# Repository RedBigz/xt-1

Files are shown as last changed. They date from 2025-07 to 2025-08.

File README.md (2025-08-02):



## IMPORTANT

- The JST PH connectors from the t-plugs to the supp. board need to have reverse connectors!

# XT-1





A modular CoreXY 3D Printer with a focus on repairability.

| [READ THE JOURNAL](./JOURNAL.md) | [READ CAD CREDITS](CAD_CREDITS.md) |
| --- | --- |

| A render of an XT-1 with a Benchy atop its bed | Gantry of an XT-1 |
| --- | --- |
| Close-up of the toolhead/bed of the XT-1 | Close-up of the bottom of the XT-1 |

## Who I am and why I made this

Hi, I'm May, a 15-year-old programmer and hardware enthusiast from Australia. I have spent the past few weeks developing a custom 3D printer based on the CoreXY motion system that allows for custom component bays to be inserted on the toolhead. I made this dovetail plug (t-plug) system to mimic the concept of [Framework](https://frame.work)'s laptop expansion bays. I believe expansion bays largely simplify repairs performed by consumers and allows for greater self-expression through custom designs that can be attached to the toolhead.

## What is this?

The XT-1 is a custom CoreXY 3D printer with two custom t-plug (as defined above) bays to transmit UART and 5V & 24V PWM signals for things such as:

- Accelerometers (not ADXL as they're SPI)
- Laser Diodes
- Fans

Here are some basic statistics for the printer:

- 2 t-plug bays
- 2WD CoreXY System
- 180x180x160 build volume
- ~360x360x420 external dimensions

# Gallery

## CAD Model

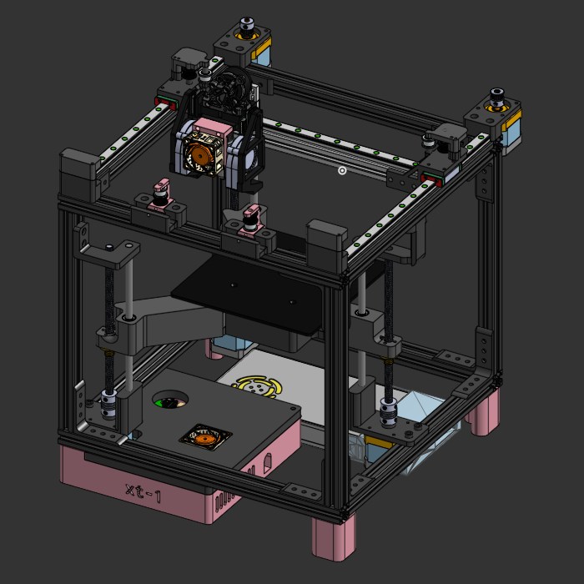
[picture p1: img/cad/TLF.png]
Top-Left-Front view of the XT-1

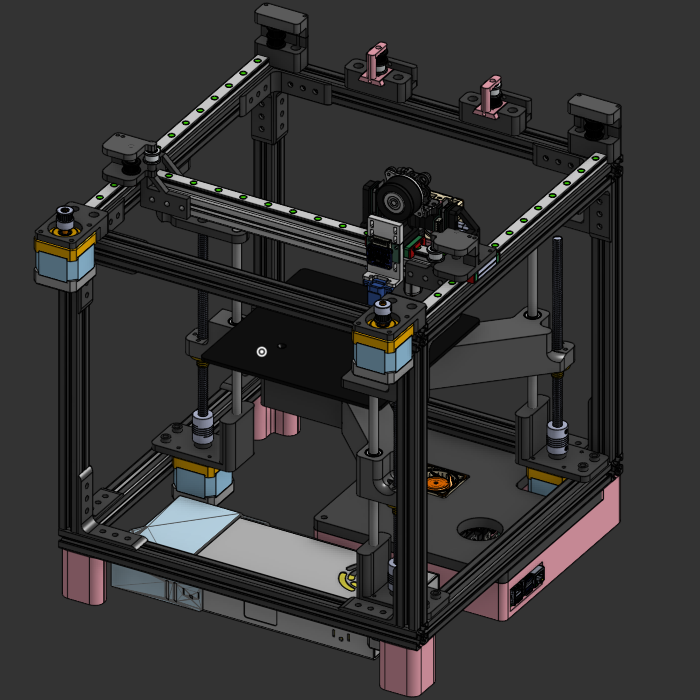
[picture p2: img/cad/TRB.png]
Top-Right-Back view of the XT-1


## Supplementary Board

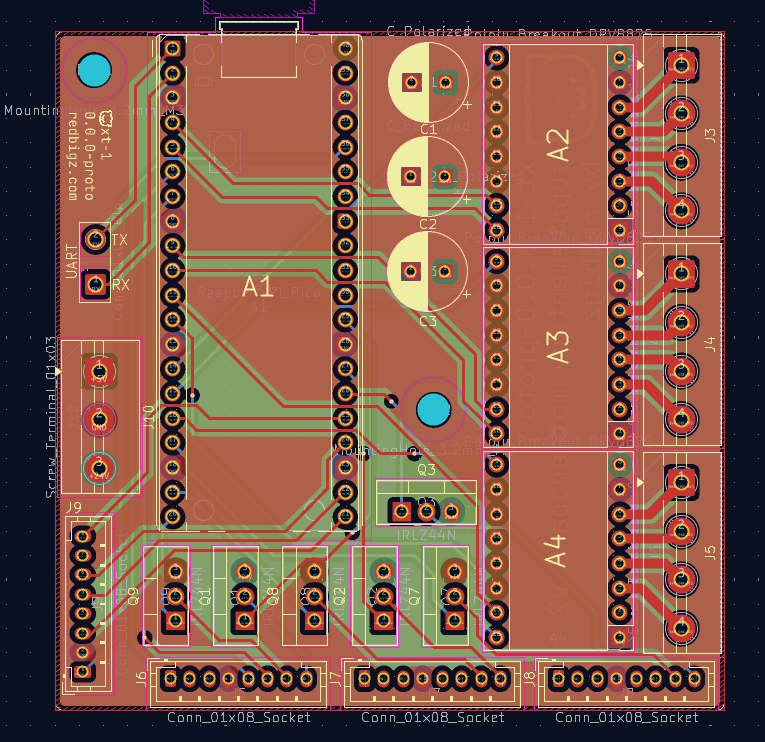
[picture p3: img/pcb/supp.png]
Pcbnew view of the Supplementary Board of the XT-1


## T-Plug

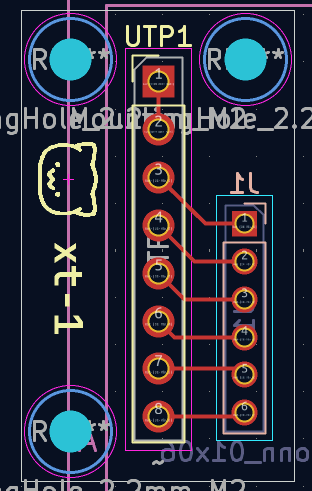
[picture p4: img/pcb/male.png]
Pcbnew view of the XT-1 male t-plug

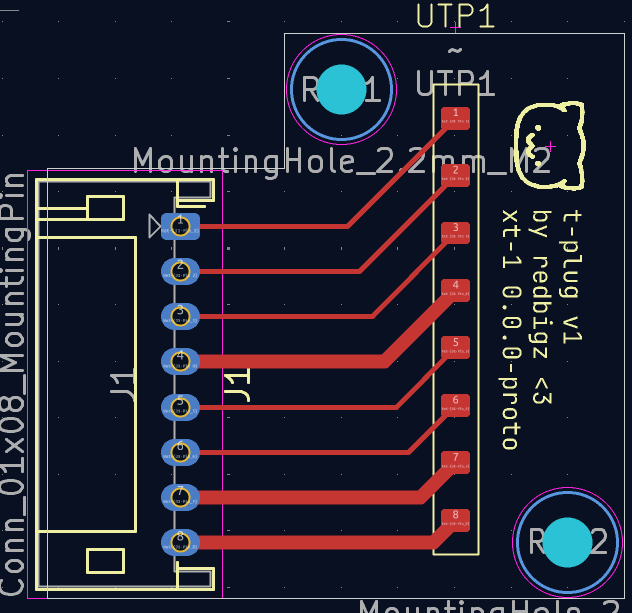
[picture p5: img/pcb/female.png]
Pcbnew view of the XT-1 female t-plug


# Building

## CAD Models

To export parts, open the model in OnShape [here](https://cad.onshape.com/documents/9bd0c3164ed27c6437ee23ee/w/6070e846ece5dc4f933b41e5/e/3b4b9a8834f82e5e0afe2787) (I would suggest plugging in your computer before downloading, the models are hundreds of megs and just rendering them has crashed my desktop RX 7800XT over 10 times when rendering the full assembly)

To find the _assembly_ in .STEP format, check the `asm` folder in this repo.

## Wiring Diagram

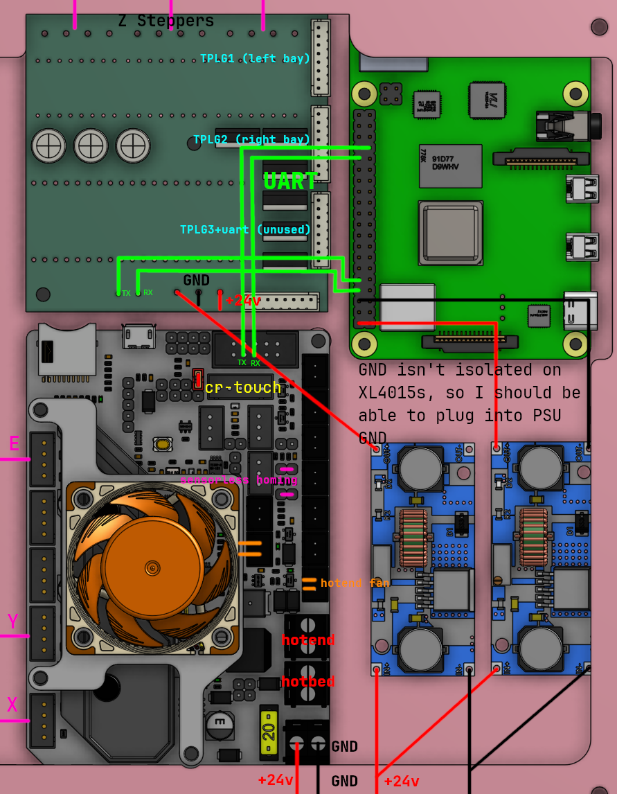
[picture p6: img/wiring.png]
An electronic wiring diagram of the XT-1


## Quick BOM

**Quick Note:** This BOM is made largely for Hack Club's [Highway grant program](https://highway.hackclub.com) and prices reference the sale price I am able to purchase each product at (as @ 29/07/2025) in AUD (with a AUD -> USD exchange rate of $0.66 per A$1).

| Manufacturer | Item | Size | Qty | Units | Unit Cost (AUD) | Cost (AUD) | Cost (USD) | Link |
| --- | --- | --- | --- | ----- | --- | --- | --- | --- |
| BIGTREETECH | BTT SKR Mini E3 V3 | - | 1 | each  | 52.51 | 52.51 | 34.66 | https://www.aliexpress.com/item/1005003519869375.html |
| JINGLIN | 5/lot 4-lead NEMA 17 | - | 1 | lot | 69.39 | 69.39 | 45.80 | https://www.aliexpress.com/item/1005008510880419.html |
| | 2/lot 5015 Turbo Fan | - | 1 | lot | 4.90 | 4.90 | 3.23 | https://www.aliexpress.com/item/32970914615.html |
| JINGLIN | 2/lot 4020 Fan | - | 1 | lot | 5.09 | 5.09 | 3.36 | https://www.aliexpress.com/item/32972111881.html |
| Ancufy | NEMA 14 + 1M cable | - | 1 | each  | 14.89 | 14.89 | 9.83 | https://www.aliexpress.com/item/1005006423228157.html |
| HighQ | 2/lot 2020 V-Slot Extrusions | 280mm | 2 | lot | 14.79 | 29.58 | 19.52 | https://www.aliexpress.com/item/1005007310271857.html |
| | | 320mm | 2 | lot | 15.89 | 31.78 | 20.97 | |
| | | 360mm | 2 | lot | 16.69 | 33.38 | 22.03 | |
| Magic Dragon | 2020 V-Slot Extrusions | 300mm | 1 | each  | 8.47 | 8.47 | 5.59 | https://www.aliexpress.com/item/1005004679698586.html |
| | MGN12 Linear Rail | 300mm | 1 | each  | 20.39 | 20.39 | 13.46 | https://www.aliexpress.com/item/1005003696820721.html |
| CHY CNC | 2/lot 8mm Linear Shaft (M4x8mm) | 200mm | 2 | lot | 16.29 | 32.58 | 21.50 | https://www.aliexpress.com/item/1005008854590053.html |
| SNWNYN | 2x MGN12H rails, 4x MGN Blocks | 200mm | 1 | lot | 34.59 | 34.59 | 22.83 | https://www.aliexpress.com/item/1005005966099152.html |
| 3D ManufacturinG | T8 Lead Screw + Nut | 200mm | 3 | each  | 5.49 | 16.47 | 10.87 | https://www.aliexpress.com/item/1005007457419235.html |
| ElectronicModule | D20L25 Lead Screw Coupler | - | 3 | each  | 2.76 | 8.28 | 5.46 | https://www.aliexpress.com/item/1005006456811778.html |
| Haldis | Gearset Kit | - | 1 | each  | 21.39 | 21.39 | 14.12 | https://www.aliexpress.com/item/1005004699143725.html |
| Lerdge | Lerdge iX 180mm Hotbed (Magnetic) | - | 1 | each  | 30.79 | 30.79 | 20.32 | https://www.aliexpress.com/item/1005005641707683.html |
| Good Luck Elec. Prod.  | 2/lot XL4015 | | 1 | lot | 6.21 | 6.21 | 4.10 | https://www.aliexpress.com/item/1005006823558141.html |
| TLZWLA | 10/lot 01x08 2.54mm Female Header Socket | - | 1 | lot | 2.16 | 2.16 | 1.43 | https://www.aliexpress.com/item/4001198421663.html |
| | 10/lot 01x20 2.54mm Female Header Socket | - | 1 | lot | 2.62 | 2.62 | 1.73 | |
| Unnamed | GY-291 ADXL345 Module | - | 1 | each  | 2.91 | 2.91 | 1.92 | https://www.aliexpress.com/item/1005007557329503.html |
| ICGOGO | 40/lot F-F DuPont Jumper Wires | 100mm | 1 | lot | 4.20 | 4.20 | 2.77 | https://www.aliexpress.com/item/1005002000655439.html |
| YouKeyi | 5/lot DRV8825 Module | - | 1 | lot | 9.99 | 9.99 | 6.59 | https://www.aliexpress.com/item/1005009321177962.html |
| USBO | IEC320 C14 Fused Switch | - | 1 | each  | 13.49 | 13.49 | 8.90 | https://www.aliexpress.com/item/4001315809458.html |
| Wurth Elektronik | 860040674004 100uF 50V | D8xL12mm | 10  | each  | 0.555 | 5.55 | 3.66 | https://au.mouser.com/ProductDetail/Wurth-Elektronik/860040674004 |
| NINDEJIN NINDEJIN | 50/lot M2x8mm Hex Wafer Head Screw | - | 1 | lot | 2.06 | 2.06 | 1.36 | https://www.aliexpress.com/item/1005008750192874.html |
| Don Eden | Pan Screws (PH) | 50pcs M3x5mm | 1 | lot | 2.82 | 2.82 | 1.86 | https://www.aliexpress.com/item/1005008709978631.html |
| | (note, 16mm screws are in place of 15mm screws due to lack of listings) | 50pcs M3x16mm | 1 | lot | 4.29 | 4.29 | 2.83 | |
| | | 50pcs M3x35mm | 1 | lot | 6.09 | 6.09 | 4.02 | |
| | | 20pcs M4x8mm | 1 | lot | 3.32 | 3.32 | 2.19 | |
| | | 10pcs M5x8mm | 7 | lot | 3.32 | 23.24 | 15.34 | |
| | | 10pcs M5x16mm | 2 | lot | 3.90 | 7.80 | 5.15 | |
| | Countersunk Screws | 20pcs M4x5mm | 1 | lot | 3.74 | 3.74 | 2.47 | |
| Hundred Years | Pan Screws (PH) | 50pcs M3x8mm | 1 | lot | 2.64 | 2.64 | 1.74 | https://www.aliexpress.com/item/1005006674754845.html |
| | | 50pcs M3x10mm | 1 | lot | 2.73 | 2.73 | 1.80 | |
| | | 50pcs M3x20mm | 1 | lot | 3.55 | 3.55 | 2.34 | |
| | | 50pcs M3x25mm | 1 | lot | 3.89 | 3.89 | 2.57 | |
| | | 50pcs M8x50mm | 1 | lot | 8.02 | 8.02 | 5.29 | |
| | Heated Inserts | 100pcs M2L2 OD3.2mm | 1 | lot | 2.89 | 2.89 | 1.91 | https://www.aliexpress.com/item/1005006967339727.html |
| | | 100pcs M3L4 OD4.2mm | 1 | lot | 2.35 | 2.35 | 1.55 | |
| CANOT | Hex Nuts | 50pcs M3 | 1 | lot | 2.19 | 2.19 | 1.45 | https://www.aliexpress.com/item/1005007593861199.html |
| | | 10pcs M8 | 1 | lot | 3.00 | 3.00 | 1.98 | |
| RTLECS | 5/lot 8P 2.54mm Pogo Pins | - | 1 | lot | 11.59 | 11.59 | 7.65 | https://www.aliexpress.com/item/4001036140528.html |
| MEAN WELL | LRS-350-24 | - | 1 | each  | 55.22 | 55.22 | 36.45 | https://au.mouser.com/ProductDetail/709-LRS350-24 |
| FreeBoom | PET Expandable Cable Sleeve | 25mmx2m | 1 | each  | 11.09 | 11.09 | 7.32 | https://www.aliexpress.com/item/1005009088606787.html |
| Unnamed | 100/lot M/F Spade Connectors | 16-14AWG | 1 | lot | 5.61 | 5.61 | 3.70 | https://www.aliexpress.com/item/1005009138598203.html |
| Unnamed | Black Copper Cable | 5m, 22AWG | 1 | lot | 3.01 | 3.01 | 1.99 | https://www.aliexpress.com/item/1005006647928006.html |
| | | 2m, 16AWG | 1 | lot | 3.68 | 3.68 | 2.43 | |
| PeoPoly | Magneto X Lancer Melt Zone Long | - | 1 | each  | 45.44 | 45.44 | 29.99 | |
| Lerdge | PEI Bed | 180x180 | 1 | each  | 11.79 | 11.79 | 7.78 | https://www.aliexpress.com/item/1005005332775787.html |
| wuhushiyu | T-Nuts | M5 / 20 Series | 150 | each  | 0.0676 | 10.14 | 6.69 | https://www.aliexpress.com/item/32814359094.html |
| | | M3 / 20 Series | 50  | each  | 0.0782 | 3.91 | 2.58 | |
| Raspberry Pi | Pi 4B (out of stock, cannot verify pricing details) | - | 1 | each  | | 0 | 0.00 | |
| | Pi Pico H | - | 1 | each  | 8 | 8 | 5.28 | https://au.mouser.com/ProductDetail/Raspberry-Pi/SC0917 |
| WGXCPP | 127/lot Heat Shrink Kit | - | 1 | kit | 4.09 | 4.09 | 2.70 | https://www.aliexpress.com/item/1005001787291963.html |
| ? | microSD Card (self sourced) | - | 2 | each  | | 0 | 0.00 | |
| Tojiato | 4/lot GT2 Idlers W6B5 | 20T | 2 | lot | 5.89 | 11.78 | 7.77 | https://www.aliexpress.com/item/1005007557987612.html |
| | | 20T Smooth | 1 | lot | 5.92 | 5.92 | 3.91 | |
| Maecoom | 3/lot GT2 Timing Pulley W6B5 | 20T | 1 | lot | 6.55 | 6.55 | 4.32 | https://www.aliexpress.com/item/1005003176136280.html |
| DFORCE Trianglelab | 6mm Timing Belt | 3000mm | 1 | each  | 19.11 | 19.11 | 12.61 | https://www.aliexpress.com/item/1005006507781085.html |
| Panda Bearings | 2/lot LM8UU Bearings | - | 2 | lot | 3.73 | 7.46 | 4.92 | https://www.aliexpress.com/item/1005007070280422.html |
| [PCB] (5/lot) {JLCPCB} | Supp. Board | - | 1 | lot | 10.62 | 10.62 | 7.01 | |
| | Male T-Plug | - | 1 | lot | 3.21 | 3.21 | 2.12 | |
| | Female T-Plug | - | 1 | lot | 3.21 | 3.21 | 2.12 | |
| | ADXL Connector | - | 1 | lot | 3.21 | 3.21 | 2.12 | |
| NEWHONGHUIDA Fastener  | 30/lot Dowel Pins | M5x20mm | 1 | lot | 7.38 | 7.38 | 4.87 | https://www.aliexpress.com/item/4000473863693.html |
| excellence | 20/lot JST PH2.0 8P Connector | Horizontal | 1 | lot | 3.16 | 3.16 | 2.09 | https://www.aliexpress.com/item/1005007755047389.html |
| | | Vertical | 1 | lot | 3.10 | 3.10 | 2.05 | |
| Unnamed | 5/lot PH 8P Ribbon Connector (Single Head) | 800mm | 2 | lot | 8.39 | 16.78 | 11.07 | https://www.aliexpress.com/item/1005006460578382.html |
| SVALID | 10/lot 4P 24AWG JST XH-2.54 Cable | 150mm | 1 | lot | 4.19 | 4.19 | 2.77 | https://www.aliexpress.com/item/1005002376525415.html |
| alinsin | 10/lot KF120 2.54mm Terminal Block | 4P | 1 | lot | 4.42 | 4.42 | 2.92 | https://www.aliexpress.com/item/1005003179482974.html |
| | | 3P | 1 | lot | 3.47 | 3.47 | 2.29 | |
| Creality | CR-Touch ABL (non-bracket) | - | 1 | kit | 38.79 | 38.79 | 25.60 | https://www.aliexpress.com/item/1005009104612536.html |
| [Filament] | 1kg PETG Black (self sourced) | | | | | 0 | 0 | |
| | 1kg PETG Pink (self sourced) | | | | | 0 | 0 | |
| | | | | | Shipping | 50.77 | 33.51 | |
| | | | | | Subtotal | 922.93 | 609.13 | |
| | | | | | +10% GST | 92.29 | 60.91 | |
| | | | | | Total | 1015.22 | 670.05 | |
| | | | | | Hack Club Grant | 530.30 | 350.00 | |
| | | | | | Out Of Pocket | 484.91 | 320.05 | |

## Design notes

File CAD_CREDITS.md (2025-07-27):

# CAD Credits

Hello! Here are the CAD files I utilised in my project:

## Voron Mods

- BTT SKR Mini E3 4010 Fan holder - https://www.printables.com/model/218425-btt-skr-mini-e3-4010-fan-holder

## Common

- NEMA 17 - https://grabcad.com/library/stepper-motor-nema-17
- NEMA 14 - https://grabcad.com/library/creality-k1-extruder-stepper-motor-cad-1

## Toolhead

- 5015 Fan - https://grabcad.com/library/radial-cooling-5015-fan-50mm-dc12v-1
- 4020 Fan - https://grabcad.com/library/noctua-fan-nf-a4x20-flx-4020-1
- Lancer Hotend - https://drive.google.com/file/d/1jBJ_lABy2rAumbZENPBUUD2NbBwpDljn/view
- ProtoXTruder - https://github.com/nhchiu/3DPrinter-Designs/tree/main/ProtoXtruder_2.0

## Gantry

- GT2 Pulley - https://grabcad.com/library/pulley-gt2-20t-b5-1
- GT2 Idler - https://grabcad.com/library/gt2-pulleys-80-tooth-20-tooth-idlers-6-9-mm-wide-1
- Smooth GT2 Idler - https://grabcad.com/library/gates-powergrip-2gt-smooth-idler-6mm-belt-12mm-od-5mm-id-e3d-1
- Linear Rails (configurator) - https://www.hiwin.de/en/tools/produktkonfiguratoren
- Linear Block - https://grabcad.com/library/mgn12-linear-guide-subassembly-configurable-rail-length-from-100-mm-to-2000-mm-in-increments-of-50-mm-1

## Bed

- LM8UU Bearing - https://grabcad.com/library/linear-bearing-lm8uu-3
- Lead Screw - https://grabcad.com/library/8mm-lead-screw-with-nut-1
- 5x8 Flexible Coupling - https://grabcad.com/library/7862-aluminum-flexible-coupling-coupler-helical-shaft-5mm-x-8mm-sunrobotics_in-1

## Electronics

### Boards

- BTT SKR Mini E3 V3 - https://grabcad.com/library/btt-e3-mini-v3-1
- Raspberry Pi 4 - https://grabcad.com/library/raspberry-pi-4-model-b-1

### Other Electronics

- XL4015 Buck Converter - https://grabcad.com/library/xl4015-1
- LRS-350 PSU - https://www.digikey.sg/en/models/7705034
- ADXL345 Module - https://grabcad.com/library/adxl345-digital-accelerometer-adafuit-breakout-board-1

### Mounts

- LRS-350 Cover - https://www.printables.com/model/53920-meanwell-lrs-350-outlet-and-cover

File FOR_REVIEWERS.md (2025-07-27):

Hi. This will be super quick, but I would like you to take these in mind when reviewing the CAD model.

**MAJOR NOTE: Please read the journal in its entirety before reviewing the model! There are a few things explained as context for the model.**

# Major "issues" you may come across

- **The part cooling fans need to be screwed in after being slid on**
  - I don't really have a big solution for this. For now, it is what it is and it can be changed at any time after approval. I believe that a solution can be implemented in the future as it is not a required feature of the printer.
- **The GT2 belts are too big on the gantry and are clipping with its neighbors**
  - This is due to a fault in sourcing CAD files. The [real listing](https://www.aliexpress.com/item/1005007557987612.html)'s height is 8.5mm and the CAD model is 10mm tall.
- **There are no mounting guides for the gantry motors**
  - You may see this if you're looking at the STEP file. The mounting guides aren't in the final assembly, they're in the "Nema Mount Guides" folder in the OnShape document.
- **The PSU mount isn't secured on the other side**
  - I planned for the electronics box to be printable in one body, and going further than the box itself wouldn't be printable. I could technically add a bracket between the box and the PSU at the screw hole but it would not solve the PSU's ability to move. I could add two screws to secure the supply, but the screw was designed to guide the PSU next to the electronic box, not to secure it.

# Minor Issues

I would prefer to be notified about minor issues (e.g. printability concerns) instead of the project being rejected. CAD files can be altered but as an unemployed student, losing 350 USD is considerably unfavourable, particularly if the reason for rejection is minor. 

By the way, the error in the gantry is from a group mate which allows me to move the gantry (the mates are in order, but it seems that some don't connect well). Additionally, the male t-plug connector will utilise 0.8mm wafer head screws due to the tight real estate (the part cooling part will house a threaded insert for the plug to be screwed into).

# BOM Differences
- I use 200mm linear guides in the BOM as they're cheaper and work the same as 300mm rails (build area is only 180x180)

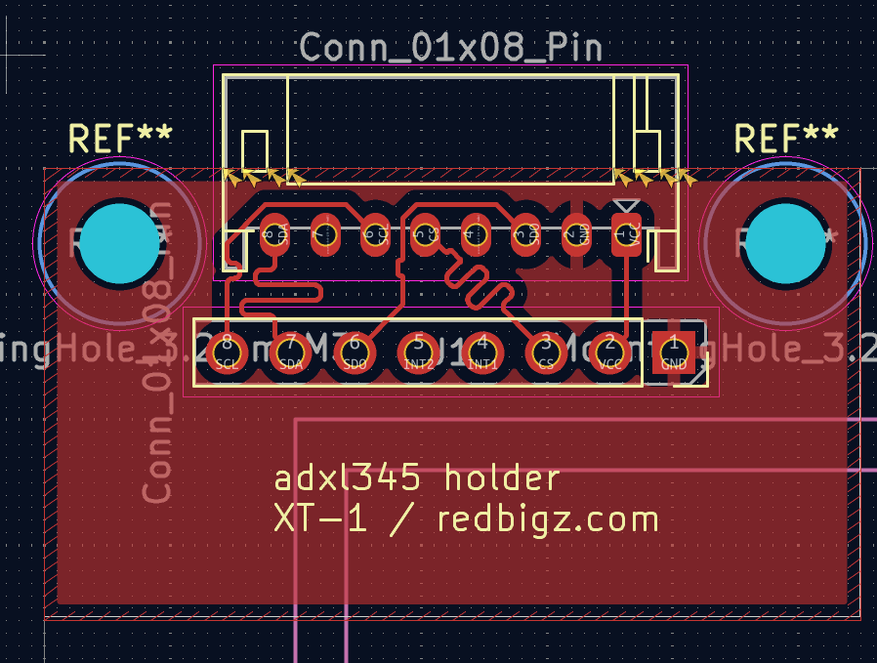
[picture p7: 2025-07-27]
img/2025/07/27/adxl2.png

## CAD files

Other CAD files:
asm/XT-1 Full Assembly.step

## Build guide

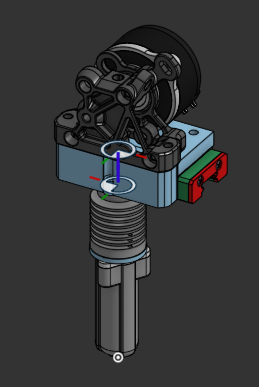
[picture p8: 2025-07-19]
img/2025/07/19/printhead.png

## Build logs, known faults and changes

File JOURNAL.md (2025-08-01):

---
title: "XT-1"
author: "redbigz"
description: "Modular CoreXY 3D Printer with a focus on repairability."
created_at: "2025-07-15"
---

**Total time:** 104 hours

# FOR REVIEWERS

If you haven't already, [read this document](./FOR_REVIEWERS.md). It outlines the differences between the CAD model and the theoretical real-life build. As you can guess, the CAD model is based on correct schematics (and placeholder CAD models from the internet don't always confine themselves to those measurements). I display all the crucial differences in this document, so I highly suggest you read it first.

# Checklist

## Pre-Design

- [x] Research
- [x] Part Picking

## Design

- [x] T-Plug
  - [x] Female Connector
  - [x] Male Connector
- [x] Toolhead _(note: excl. part cooling fans as they're modules)_
  - [x] Hotend
  - [x] Extruder
  - [x] Electronics
- [x] Gantry
- [x] Bed
- [x] Base
  - [x] Base Extrusions
- [x] Modules
  - [x] 5015 Part Cooling Fan
- [x] Motherboard
  - [x] Schematic
  - [x] PCB

### Extra Features I Want

- [x] Belt Tensioner

# Table Of Contents (by Date)

- [2025-07-15](#2025-07-15---research)
- [2025-07-16](#2025-07-16---more-research--pcb-design)
- [2025-07-17](#2025-07-17---starting-pcb-design)
- [2025-07-18](#2025-07-18---cad-designing-and-fixes)
- [2025-07-19](#2025-07-19---toolhead)
- [2025-07-20](#2025-07-20---more-toolhead)
- [2025-07-21](#2025-07-21---fan-ducts-was-pretty-unproductive)
- [2025-07-22](#2025-07-22---gantry)
- [2025-07-23](#2025-07-23---gantry--supplementary-motherboard)
- [2025-07-24/25](#2025-07-2425---bed--supplementary-motherboard)
- [2025-07-26](#2025-07-26---electronics-and-fixes)
- [2025-07-27](#2025-07-27-minor-fixes--additions)
- [2025-07-28/29](#2025-07-2829---journaling)

# 2025-07-15 - Research

I've been researching today about 3D printer parts and brainstorming all the logistics behind this modular system.

**Estimated time:** 4 hours

## Designing Factors

- I want my printer to be easily user-repairable without any issues (taking inspiration from Framework devices)
- Single/two common screw heads used throughout the build (I'm thinking of Torx T10 or T5) \*\*(NOTE FROM THE FUTURE: Turns out it's hard to source Torx screws! I'm going with Philips/Hex heads)
- _Attempting_ to do a heated bed
- Controlled via a socketed Pi CM3/CM4 (Klipper)
- SUPER EASY TO DISASSEMBLE!
- A triple module bay on the toolhead which can be hotswapped while the printer is on (for e.g. filament sensor, RGB, resonance tester, camera, laser cutter :3), using pogo pins and a dovetail system

## Part Ideas

### Base

- As suggested by Evan Le, I'm going with 2020 T-shape Aluminium Extrusions
- MGN12H or MGN9H rails
- CoreXY gantry

## Electronics Ideas

### Internals

- Socketed Pi CM3/CM4 on a custom daughterboard
- Socketed RP2040-based (custom?) motherboard
- TMC2209 Steppers
- Mean Well LRS-350-24 PSU

### Toolhead

- CR-Touch
- Lancer Melt Zone Long Hotend
- Nema 17 Steppers
- 3 Dovetail Bays for fans & expansions

# 2025-07-16 - More research & PCB design

**Estimated time:** 3 hours

## On Pi Compute Modules

For designing a motherboard with the Pi 4, I'll need to solder Hirose `DF40C-100DS-0.4v` connectors, which are SMD.

## Designing the PCB (and failing)

I got about this much done in terms of an Ethernet connection (MagJack) before calling quits. **I'm now deciding to run a regular Raspberry Pi 4 and use a stock motherboard such as the BTT SKR MINI.**

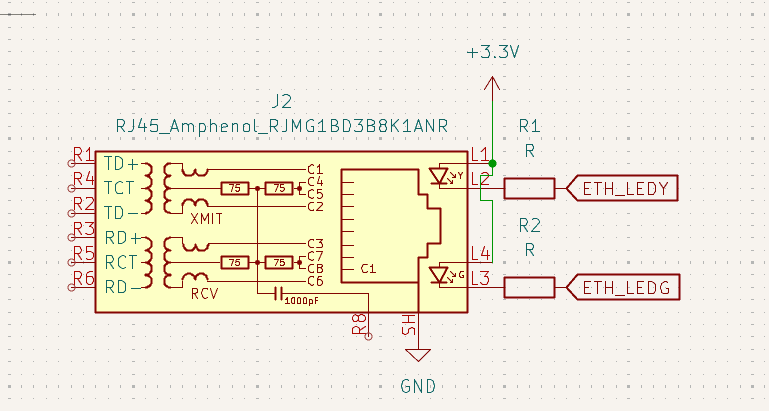
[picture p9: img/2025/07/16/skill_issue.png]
epic fail

<br>
Figure 1 - _After hours of reading datasheets, all I could make was this._

# 2025-07-17 - Starting PCB design

**Estimated time:** 5 hours

## The Dovetail Plug system

(also known as the tail plug system 😬😬😬, i'll be shortening it to t-plug from here on out)

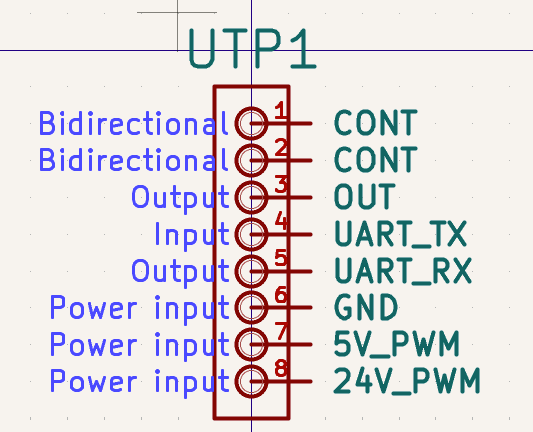
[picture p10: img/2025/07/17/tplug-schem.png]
image of the glorious t-plug schematic

<br>
Here is the system for swappable toolhead attachments. I've decided on these main points:

- The CR-Touch will NOT use the attachment system as it requires multiple grounds and for the Z stepper to be on the same MCU (not happening)
- The 5V and 24V PWM inputs will be turned on as soon as both **CONT** pins are connected (in the event of a connection)
- One UART bus will be connected for the center module (the Pi Pico only has two UART buses and one needs to be used to connect to the Linux Pi)

I took the time to figure out KiCad and make the necessary symbols and footprints for the t-plug.

Here is the female PCB, using a JST-PH to communicate with the extruder board:
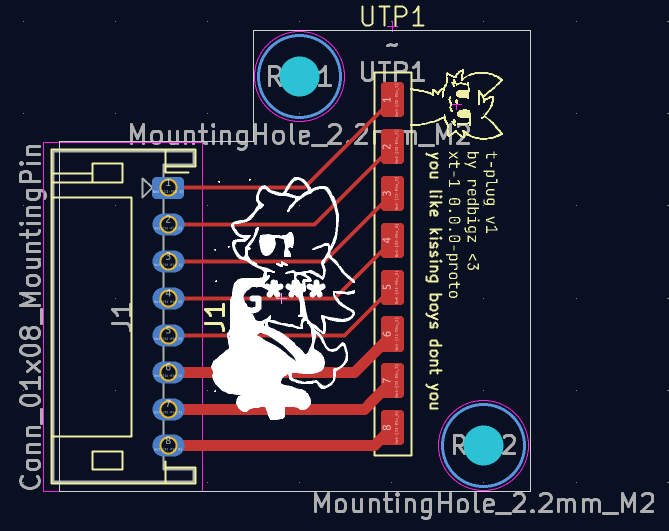
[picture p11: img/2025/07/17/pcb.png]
t-plug female pcb

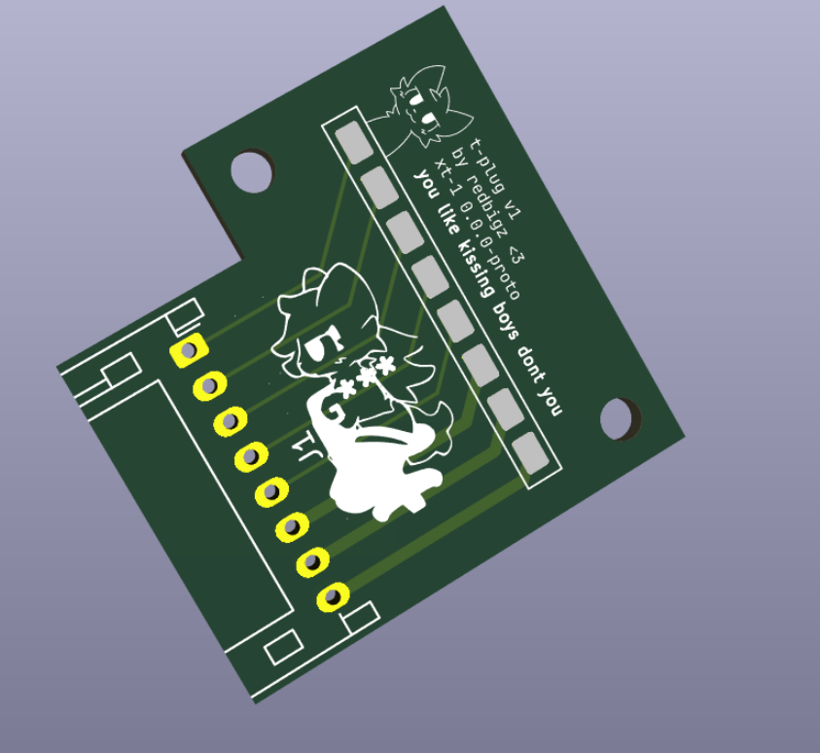
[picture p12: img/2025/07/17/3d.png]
t-plug female pcb but in 3d :3

<br>
_look at my princess isnt she bootiful_

# 2025-07-18 - CAD Designing and fixes

**Estimated time:** 6 hours

## Plug Design

i've got the thing in OnShape now, and designed a dovetail system for keeping the pogo pins in place.

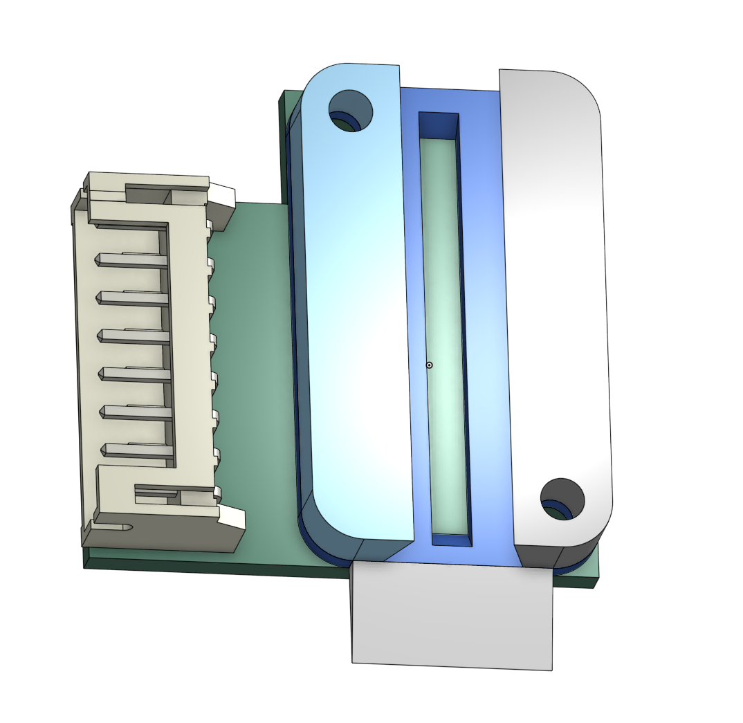
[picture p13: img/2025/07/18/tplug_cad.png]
t-plug in cad!


## Base Design

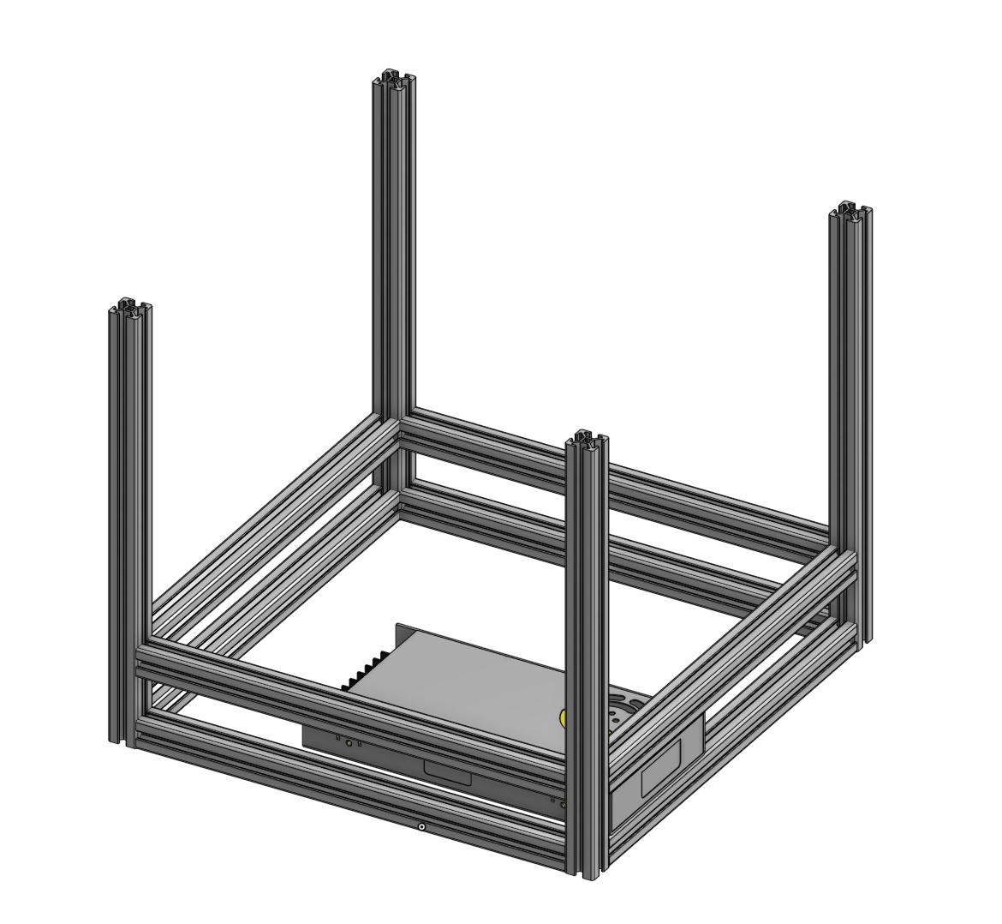
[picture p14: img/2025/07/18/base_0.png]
base number 0


## Fixes

### Shorting avoidance on the T-plug

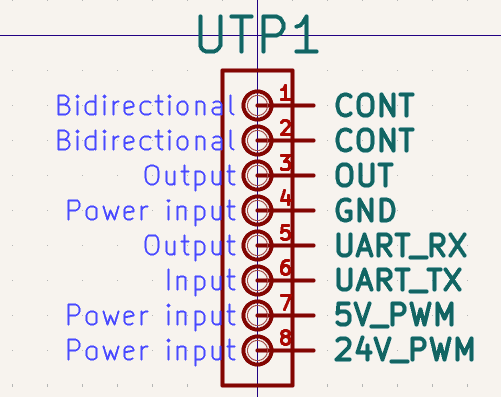
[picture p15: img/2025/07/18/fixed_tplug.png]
fixed t-plug schematic


I moved ground away from the powered pads to avoid pogo pins shorting due to proximity when sliding. I also changed the pad size of the female receptacle to avoid such proximity (as the pins are 0.9mm and the gap was 0.5mm):

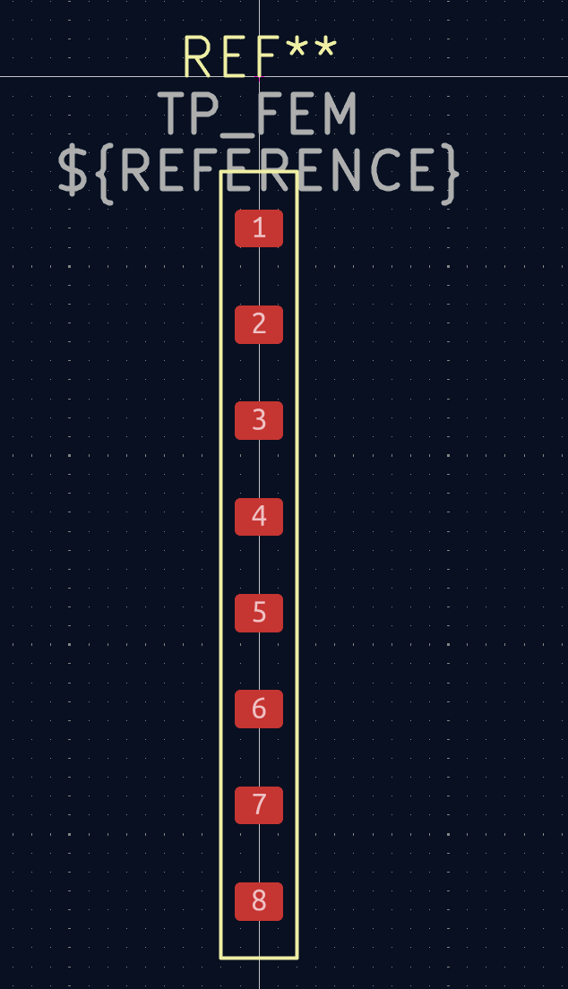
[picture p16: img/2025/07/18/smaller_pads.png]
smaller pads!


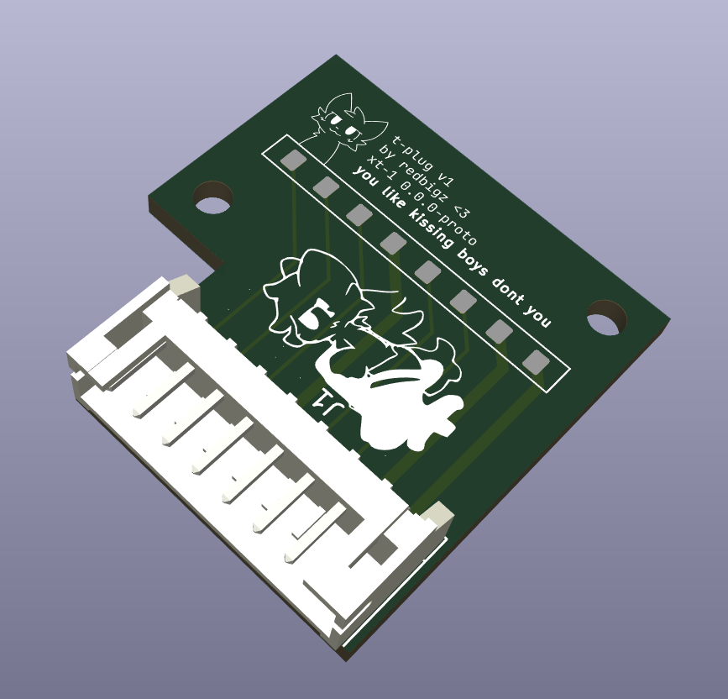
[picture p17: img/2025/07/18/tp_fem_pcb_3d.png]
tplug female pcb, fixed


# 2025-07-19 - Toolhead

**Estimated time:** 8 hours

I'm pretty tired so I'll cut to the chase here. I made about 70% of the toolhead, and the only things left are the electronics and fans.

Using a [ProtoXtruder](https://github.com/nhchiu/3DPrinter-Designs/tree/main/ProtoXtruder_2.0) for the extruder, with a Nema 14 36mm Round Pancake motor (10T gear)

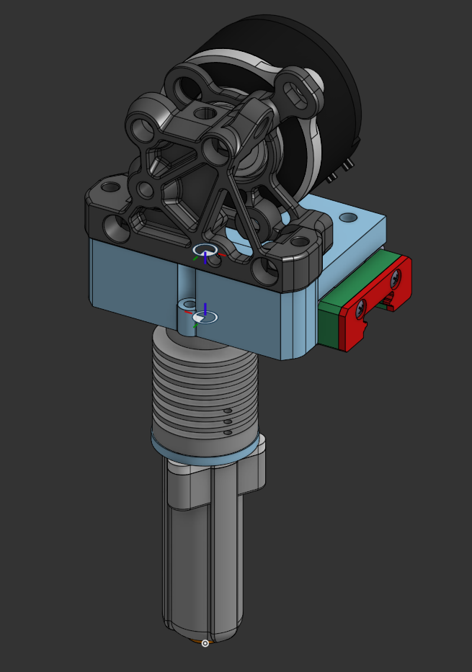
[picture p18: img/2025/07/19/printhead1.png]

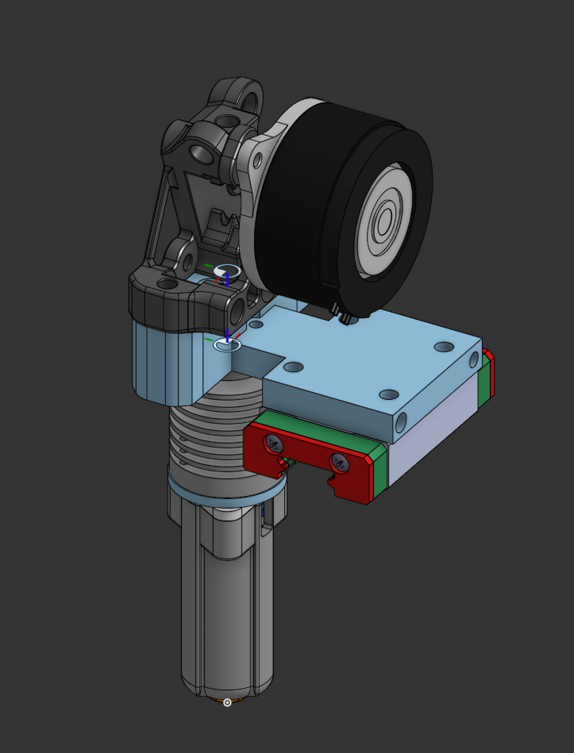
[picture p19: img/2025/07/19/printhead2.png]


UPDATE: Fixed some heights to make it stronger:

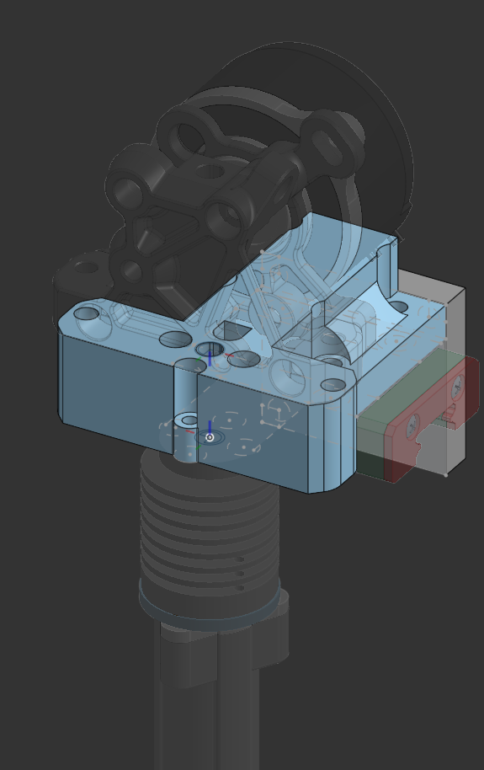
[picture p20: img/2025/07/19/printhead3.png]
toolhead fixed


# 2025-07-20 - More Toolhead

**Estimated time:** 7 hours

## Finished\* Toolhead

I've added:

- a 4010 fan (Noctua)
- a belt holder (which doubles as a CR-Touch mount)
- two t-plug bays (I know I said three but there isn't much of a use with three considering the CR-Touch isn't a module)

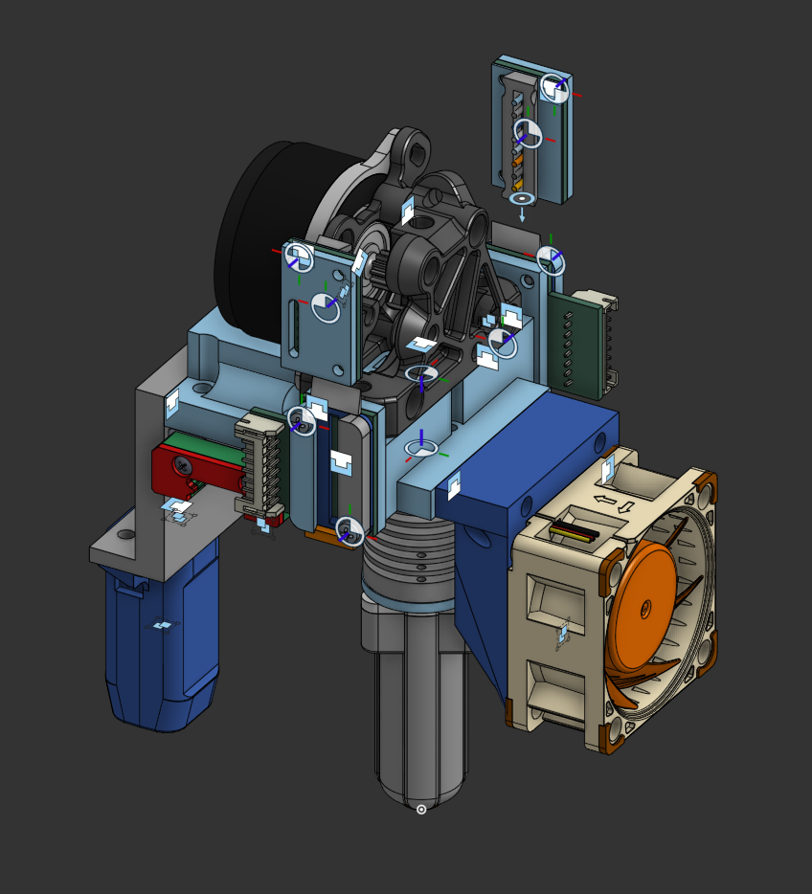
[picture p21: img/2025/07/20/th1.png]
the finished toolhead, apart from modules.

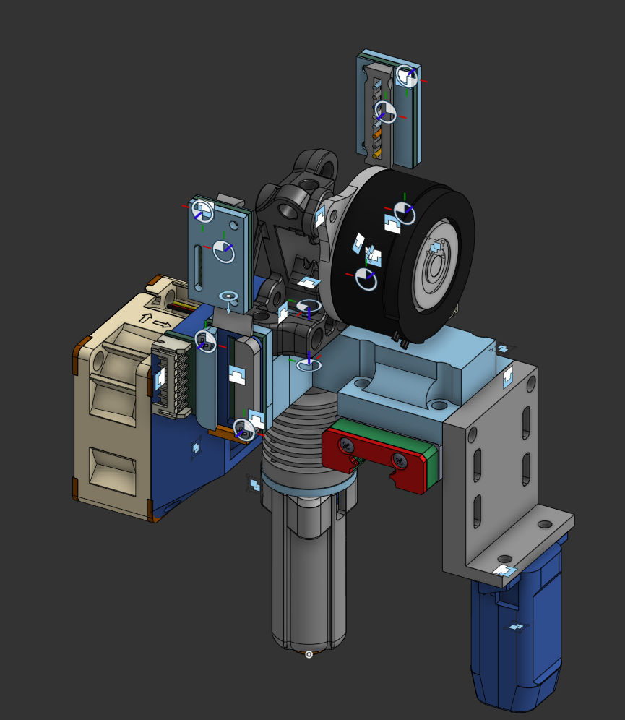
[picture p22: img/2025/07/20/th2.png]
the back side of the toolhead


Speaking of which, here is the male t-plug connector:

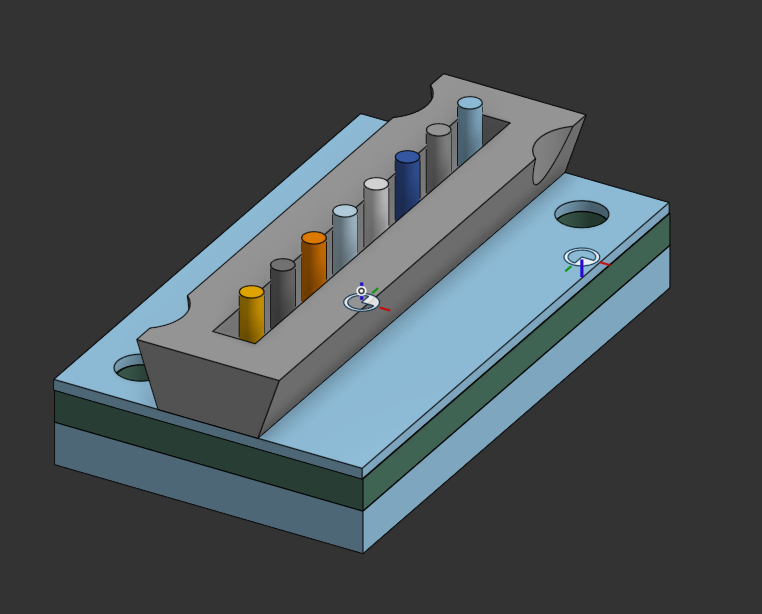
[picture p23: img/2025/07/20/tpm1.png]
male t-plug connector

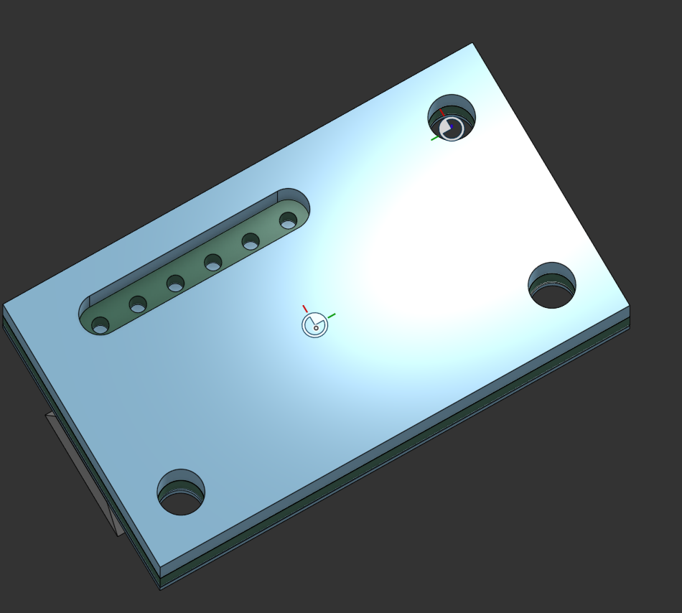
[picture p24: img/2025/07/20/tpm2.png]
back side of the male t-plug

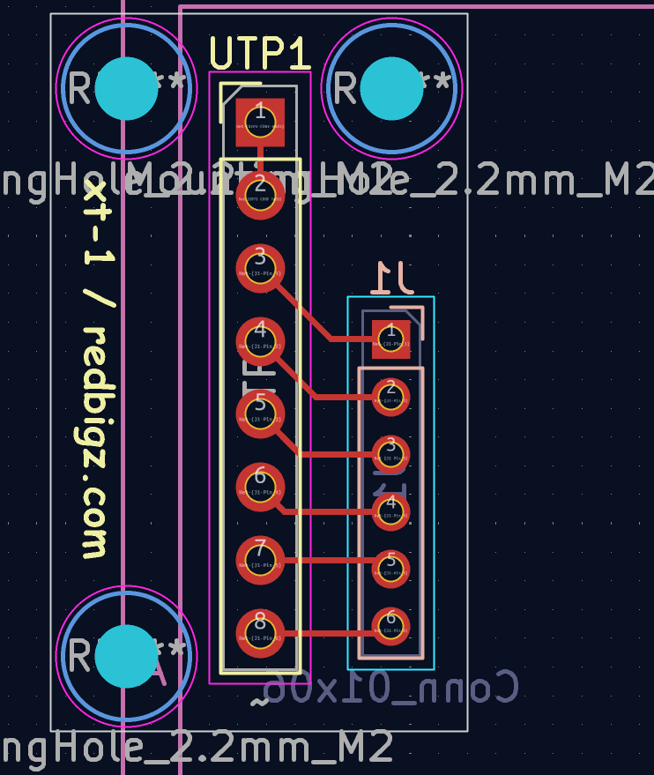
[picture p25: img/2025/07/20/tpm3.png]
pcb screenshot of the male t-plug

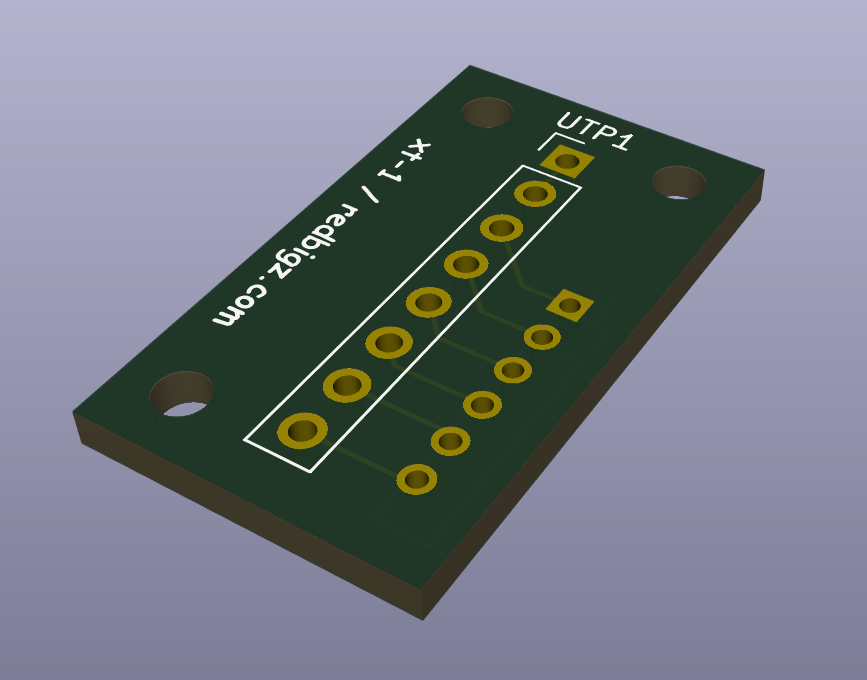
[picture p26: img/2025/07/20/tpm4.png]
3d view of the male t-plug in kicad


There's just enough clearance for the connection to the female bay (1.5mm) :3

# 2025-07-21 - Fan Ducts! (was pretty unproductive)

**Estimated time:** 5 hours

Today was pretty unproductive. I only managed to get two 5015 fan modules done. Due to the sliding mechanism, the fan module won't slide in unless the fans are screwed in after the frame is slid in.

You gotta admit it looks cool though:

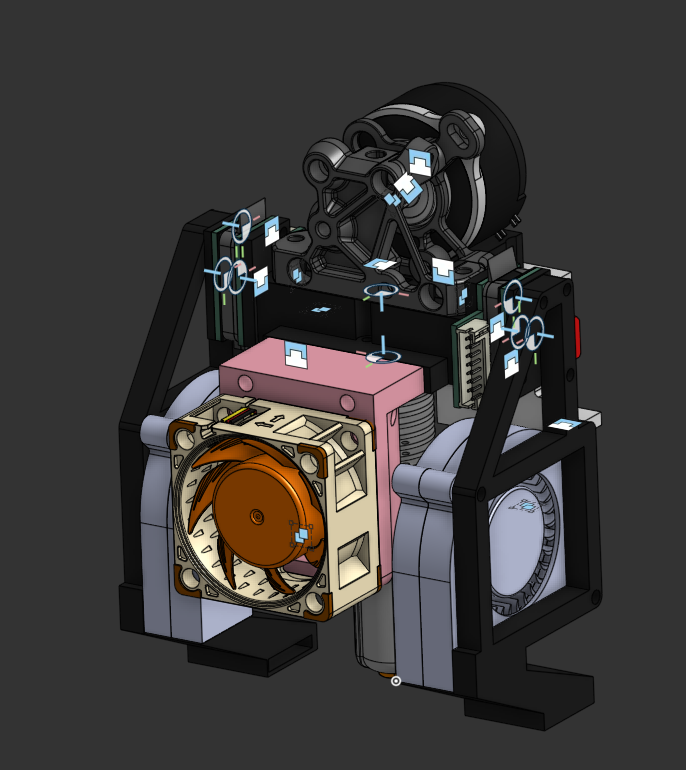
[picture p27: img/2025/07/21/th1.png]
cool toolhead


# 2025-07-22 - Gantry

**Estimated time:** 6 hours

I got a really productive session in CAD today. I've got the toolhead set up on a 360x360 gantry, along with the motor mounts and X axis idlers.

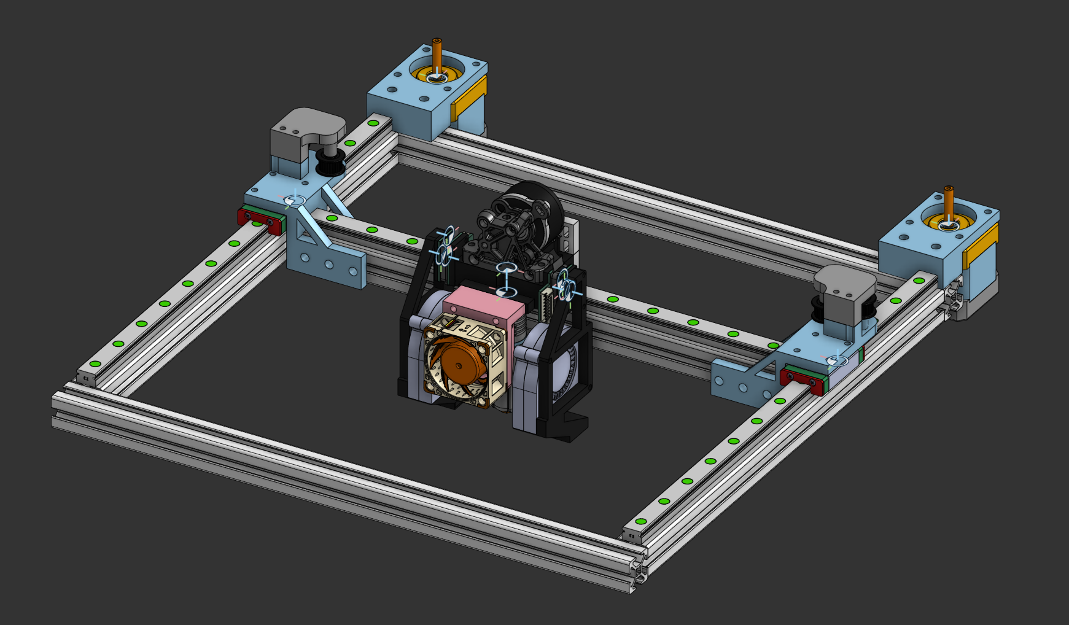
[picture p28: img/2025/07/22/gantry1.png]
the gantry!


Here's the dual-idler design I came up with (took some inspiration from other CoreXY printers):

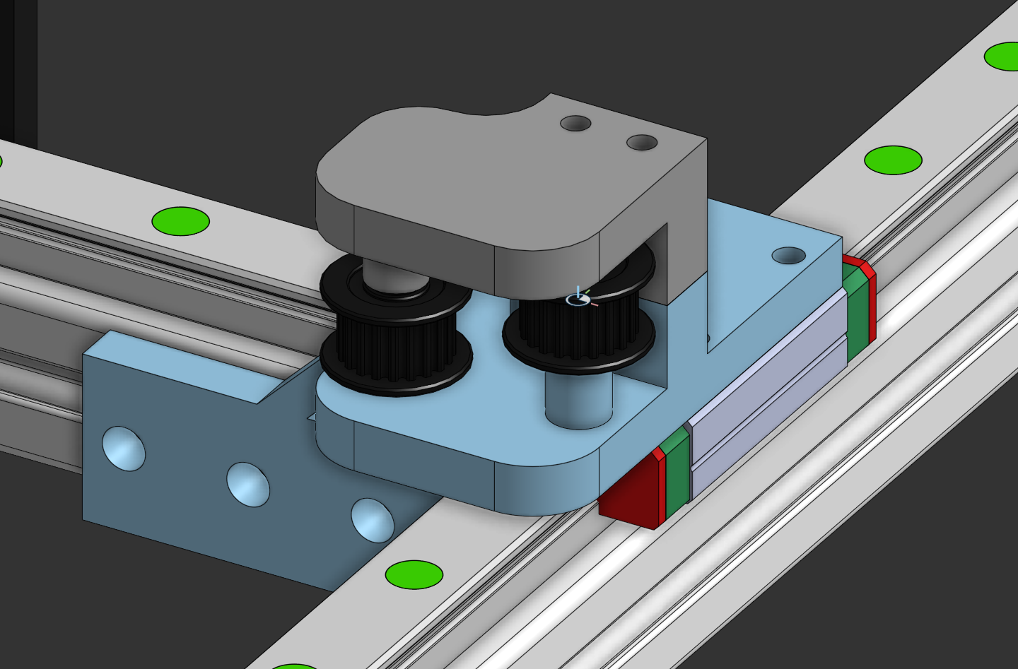
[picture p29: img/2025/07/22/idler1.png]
an x-axis dual-idler mount


I'm basing my belt setup based on this image found in the [Anicept Vex CoreXY](https://highway.hackclub.com/guides/anicept-vex-corexy) guide in Highway:

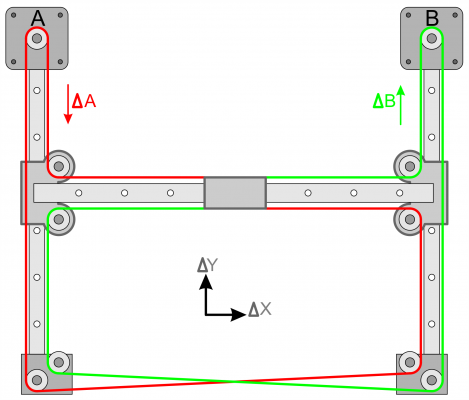
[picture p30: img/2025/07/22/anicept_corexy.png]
anicept corexy image


# 2025-07-23 - Gantry & (Supplementary) Motherboard

**Estimated time:** 8 hours

I'm pretty tired (again), so I'll just recount what I did.

I finished my gantry in its entirety:

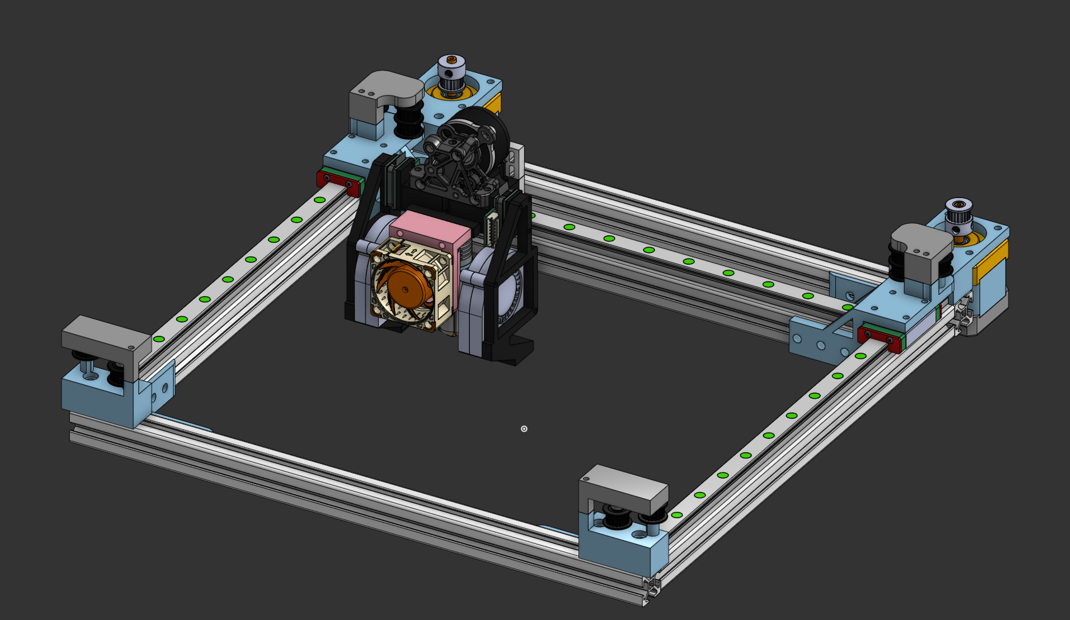
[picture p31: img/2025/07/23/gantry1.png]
finished gantry


I made custom mounts for all the idlers, and worked out a belt path that _barely_ works. I'll tweak it while building the thing, since I'm starting to run out of time before Highway ends. I've worked out a gantry area of about 190x180 for the toolhead.

Also, I've started work on a supplementary motherboard (yep, this lil guy has two moms!). It holds three limited ports for the t-plug system (lacking CONT due to a gpio shortage), with one having access to the secondary UART bus. Here's the finished schematic:

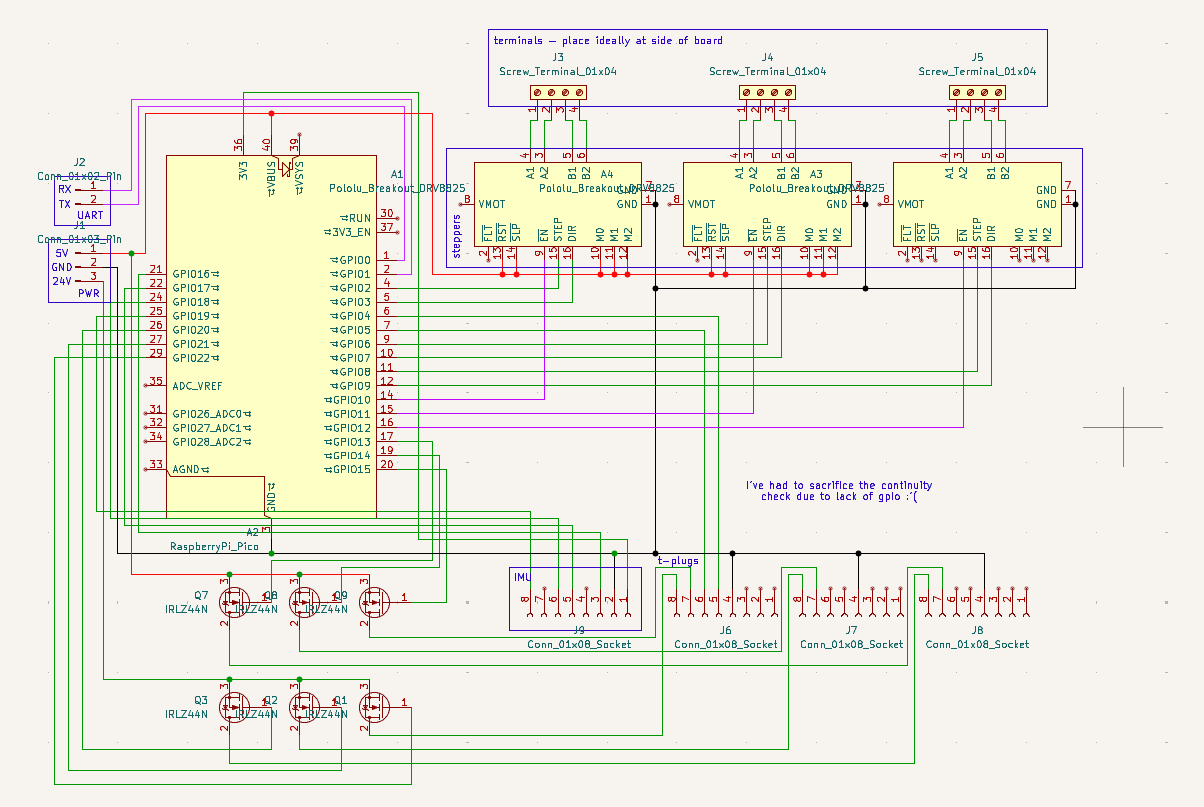
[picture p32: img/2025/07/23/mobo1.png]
motherboard schematic


# 2025-07-24/25 - Bed & Supplementary Motherboard

**Estimated time:** 20 hours

## Bed

I've considered using linear rods with LM8UU bearings (the small ones), along with lead screws. I've decided to not use kinematic mounting as it'll add time to a project where not a lot of time is left to submit. I'm using a hotplate from the Lerdge iX cantilever printer as it fits my print size.

Here's the bed:

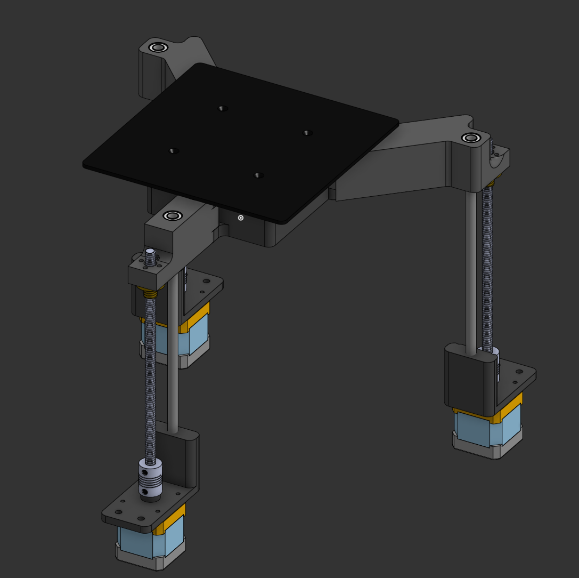
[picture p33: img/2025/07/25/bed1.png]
mostly finished bed


I've also taken the time to assemble the bed and gantry into a full assembly:

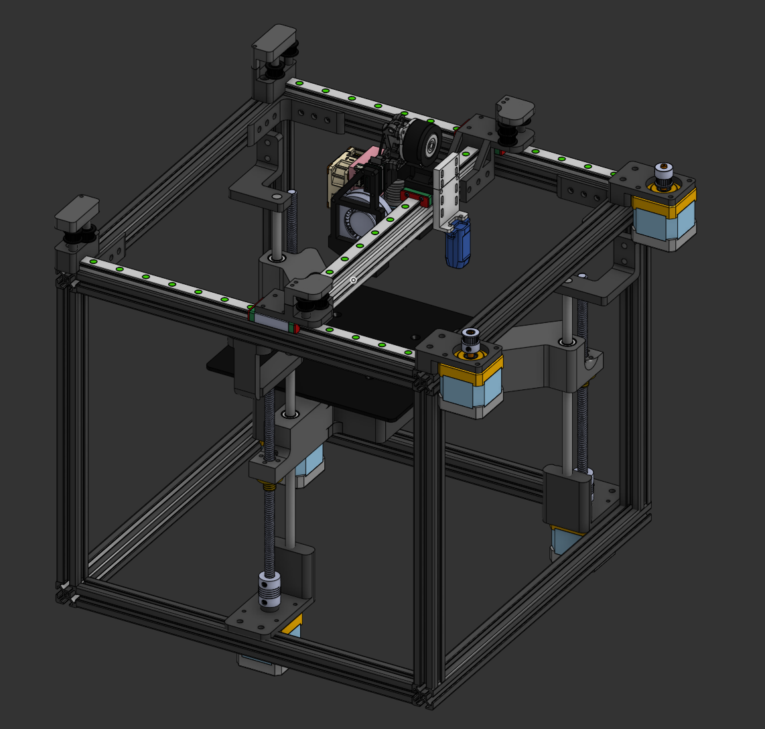
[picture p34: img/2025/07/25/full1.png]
full assembly


I've also turned the motherboard schematic into a PCB (with a little help from freerouting :3):

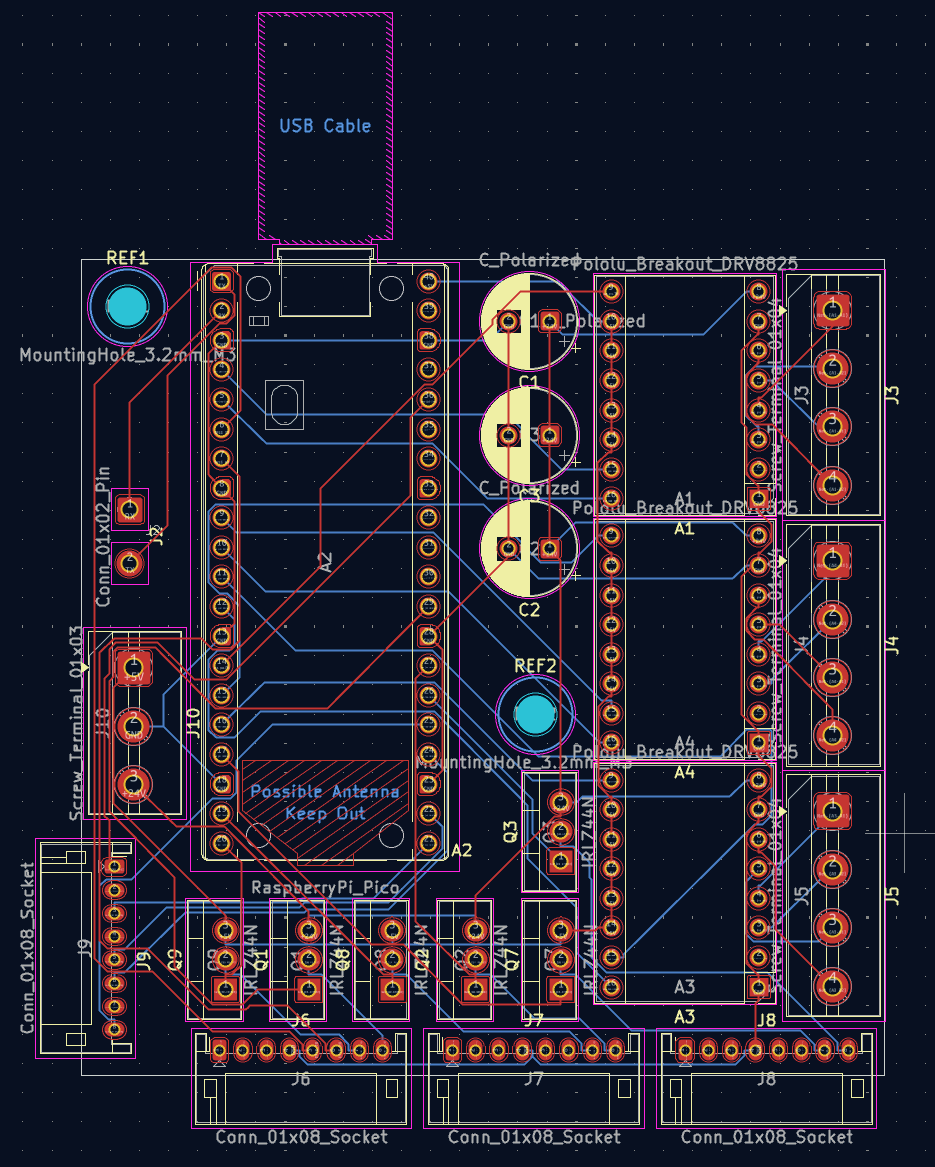
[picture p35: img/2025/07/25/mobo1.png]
motherboard pcb


# 2025-07-26 - Electronics and fixes

**Estimated time:** 12 hours

## Fixes

### T-Plug Receptacles

I fixed a collision issue with screws on the t-plug receptacles colliding with the male plug. I fixed this by adding an indent for pan screws.

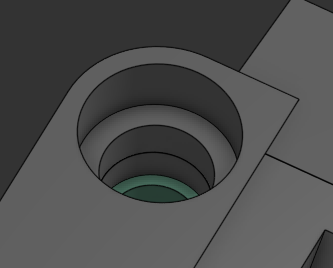
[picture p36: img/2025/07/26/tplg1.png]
indentation on the fixed t-plug


### Gantry

When working on my to-fix list, I noticed that:

1. my gantry was fairly uneven
2. nothing was perpendicular, so when the carriage moves the belt tension will change (leading to snapping or stretching).

You can see these issues prevalent here:

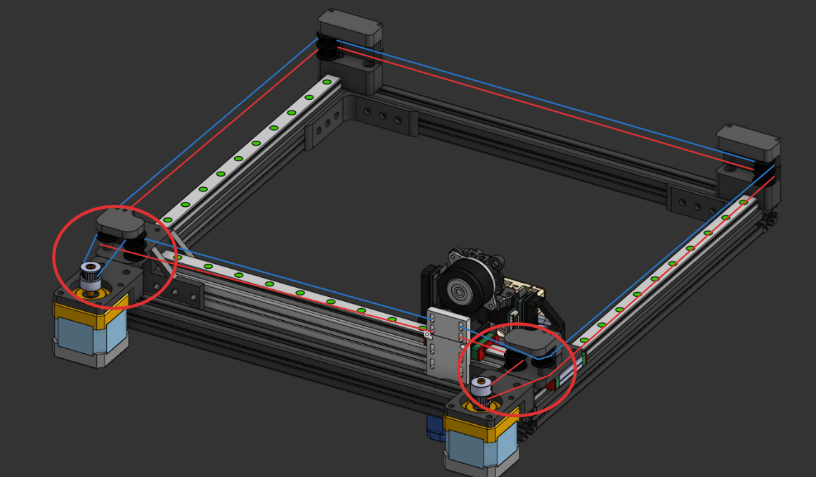
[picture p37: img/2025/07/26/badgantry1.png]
borked gantry


As you can see in this diagram by [Mark Rehorst](https://drmrehorst.blogspot.com/2018/08/corexy-mechanism-layout-and-belt.html), the critical CoreXY components need to be perpendicular:

corexy diagram

_Original Caption: UMMD's coreXY mechanism. All the pulleys are stacked, and belt segments A-H are parallel to the guide rails._

I mitigated this by redesigning the gantry correctly:

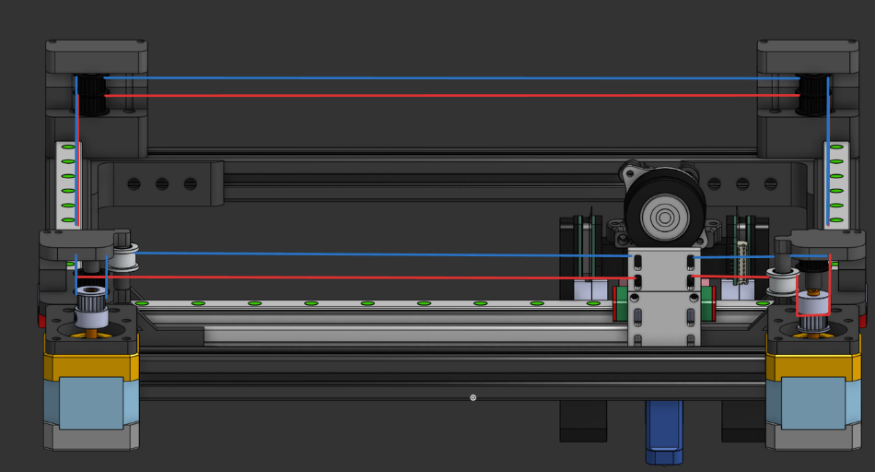
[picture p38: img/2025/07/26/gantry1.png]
fixed gantry


## Additions

### Electronics

On one of my feet, I've added a compartment holding my Raspberry Pi, SKR, and Supplementary Motherboard:

electronics compartment

I've also added a singular screw mount for holding the PSU. It's not intended to be secured, but just to position the PSU (at least for now).

psu mount pic #1
psu mount pic #2

_You can also see in the first photo that I'm using a PSU enclosure. You can find the model and its author [here](https://www.printables.com/model/53920-meanwell-lrs-350-outlet-and-cover) (thanks pmichaud!)._

## Full Screenshot

Here's the final build (at least until I make the belt tensioner):

full screenshot of the printer

# 2025-07-27 Minor Fixes & Additions

**Estimated time:** 9 hours

## Belt Tensioner

I've finally implemented a belt tensioner system (although somewhat jank).

belt tensioners mounted on gantry

It uses a dovetail system with a bolt and nut holding it in place.

 

Due to a possible collision in the tensioner with the belt, I've opted to add smooth idlers to the opposite belt being tensioned (as seen in the first photo). However, this causes the other belt to be tensioned as well - offset by the diameter of the inner part of the pulley. Having two tensioners allows the user to counteract this effect.

## Electronics Lid & Mobo Fan Mod

_Hi! For this segment I'm utilising [this](https://www.printables.com/model/218425-btt-skr-mini-e3-4010-fan-holder) fan mod designed for a VORON V0.1 printer. Thanks 3DMegoldasok!_

I've firstly added a lid for the electronics box, secured with three M3 screws. There are two cutouts, one for a fan and one for the main stepper motor.

electronics lid

I've placed the fan mod described above down on the main board:

fan mod

Additionally, I've added exhaust holes for the hot air to escape:

grilles on the side of the box

## Minor Fixes

These aren't on screenshots in the journal, but here are some minor fixes I implemented for consistency:

- Mounting screw shafts for objects on top of the gantry extrusions have been reduced to 10mm, allowing for M5x15 screws to be used throughout the gantry. This has also happened on the toolhead, but just to make the screw size a bit more understandable (not at exactly 10mm though).
- Gantry object screw shafts have been inspected and fixed (I had found holes in some areas of pulley holders)

A lot of the time from this journal section was devoted to working on the BOM. I should be done with it tomorrow.

# 2025-07-28/29 - Journaling

**Estimated time:** 11 hours

I've worked on the BOM for the two days this entry is allocated too. I also fixed a few things, which I'll list now:
- I've made some screws more universal throughout the build (you'll see holes and raised bits on some of the stepper/gantry mounts to save screw usage)
- I've fixed some mounting issues with the bed in CAD (wasn't being displayed right)

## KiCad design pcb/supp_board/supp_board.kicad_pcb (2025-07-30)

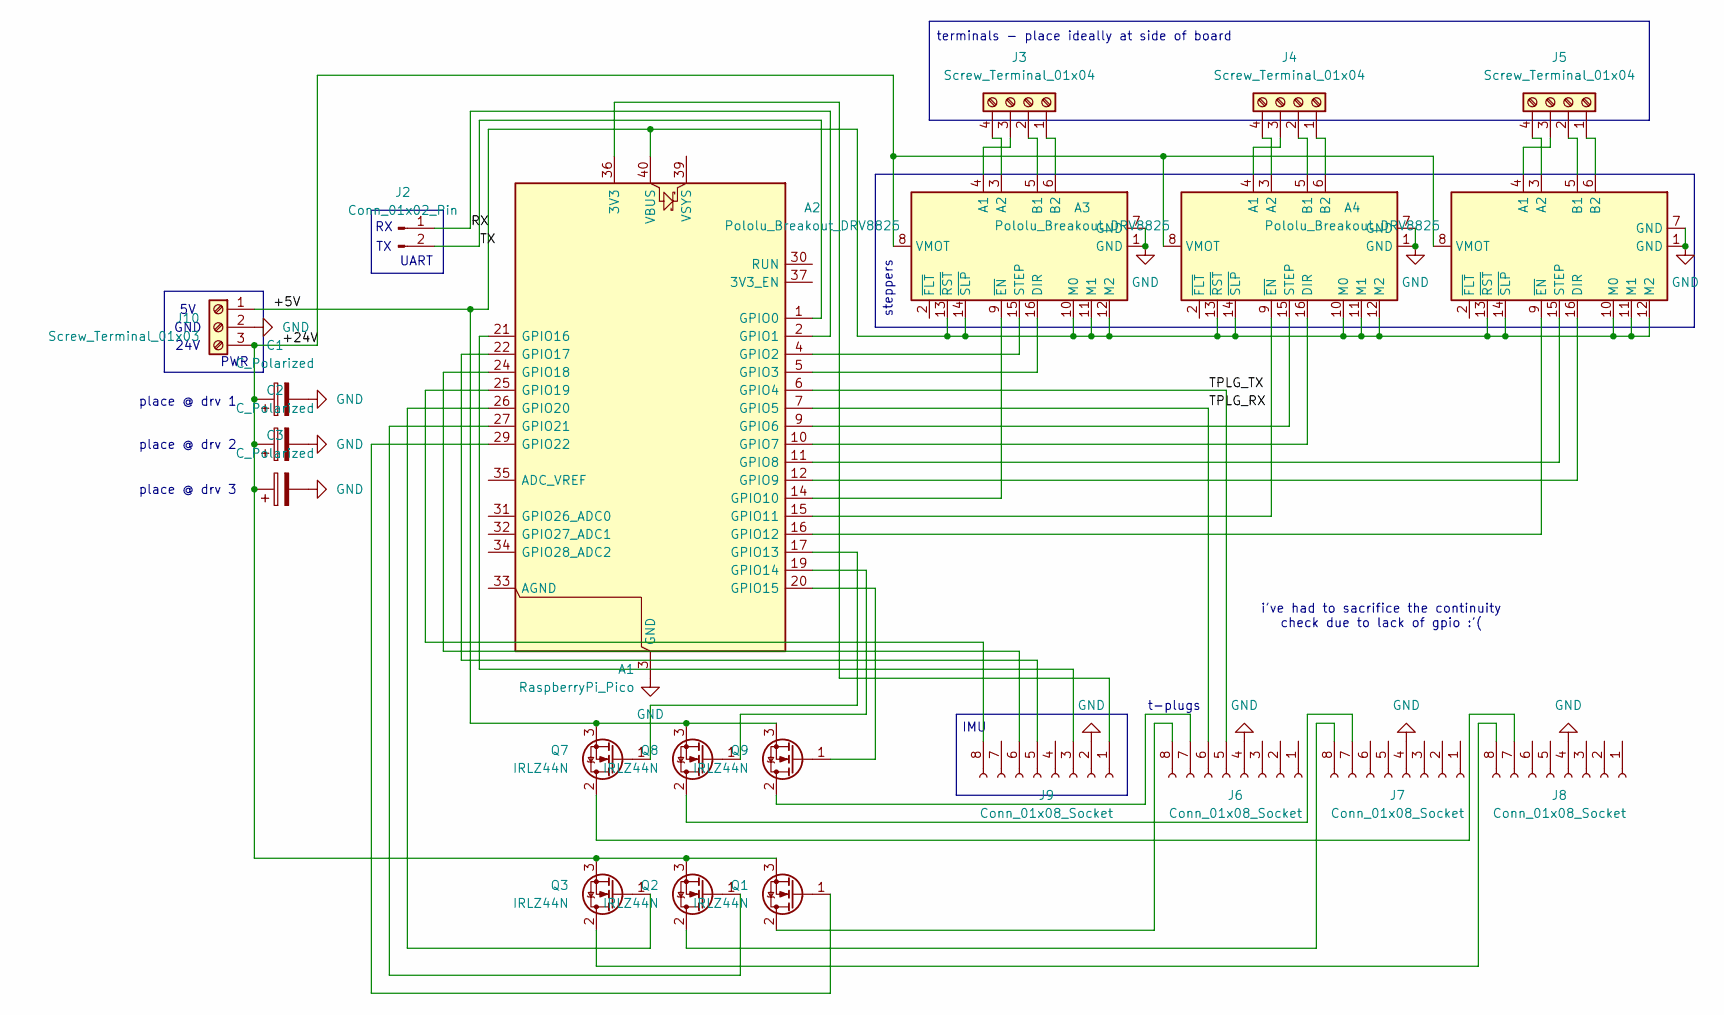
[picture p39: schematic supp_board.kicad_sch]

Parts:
A1: RaspberryPi_Pico; RaspberryPi_Pico_Common_THT
A2, A3, A4: Pololu_Breakout_DRV8825; Pololu_Breakout-16_15.2x20.3mm
C1, C2, C3: C_Polarized; CP_Radial_D8.0mm_P3.50mm
J2: Conn_01x02_Pin; SolderWire-0.5sqmm_1x02_P4.6mm_D0.9mm_OD2.1mm
J3, J4, J5: Screw_Terminal_01x04; TerminalBlock_MaiXu_MX126-5.0-04P_1x04_P5.00mm
J6, J7, J8, J9: Conn_01x08_Socket; JST_PH_B8B-PH-K_1x08_P2.00mm_Vertical
J10: Screw_Terminal_01x03; TerminalBlock_MaiXu_MX126-5.0-03P_1x03_P5.00mm
Q1, Q2, Q3, Q7, Q8, Q9: IRLZ44N; TO-220-3_Vertical

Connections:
/+5V: A1.40 (VBUS), A2.10 (M0), A2.11 (M1), A2.12 (M2), A2.13 (~RST), A2.14 (~SLP), A3.10 (M0), A3.11 (M1), A3.12 (M2), A3.13 (~RST), A3.14 (~SLP), A4.10 (M0), A4.11 (M1), A4.12 (M2), A4.13 (~RST), A4.14 (~SLP), J10.1, Q7.3 (S), Q8.3 (S), Q9.3 (S)
/+24V: A2.8 (VMOT), A3.8 (VMOT), A4.8 (VMOT), C1.1, C2.1, C3.1, J10.3, Q1.3 (S), Q2.3 (S), Q3.3 (S)
/RX: A1.2 (GPIO1), J2.1; also elsewhere on the board
/TPLG_RX: A1.7 (GPIO5), J6.6
/TPLG_TX: A1.6 (GPIO4), J6.5
/TX: A1.1 (GPIO0), J2.2; also elsewhere on the board
GND: A1.3 (GND), A1.8 (GND), A1.13 (GND), A1.18 (GND), A1.23 (GND), A1.28 (GND), A1.38 (GND), A2.1 (GND), A2.7 (GND), A3.1 (GND), A3.7 (GND), A4.1 (GND), A4.7 (GND), C1.2, C2.2, C3.2, J6.4, J7.4, J8.4, J9.2, J10.2
unnamed: A1.36 (3V3), J9.1
unnamed: A1.4 (GPIO2), A2.15 (STEP)
unnamed: A1.5 (GPIO3), A2.16 (DIR)
unnamed: A1.9 (GPIO6), A3.15 (STEP)
unnamed: A1.10 (GPIO7), A3.16 (DIR)
unnamed: A1.11 (GPIO8), A4.15 (STEP)
unnamed: A1.12 (GPIO9), A4.16 (DIR)
unnamed: A1.14 (GPIO10), A2.9 (~EN)
unnamed: A1.15 (GPIO11), A3.9 (~EN)
unnamed: A1.16 (GPIO12), A4.9 (~EN)
unnamed: A1.17 (GPIO13), Q7.1 (G)
unnamed: A1.19 (GPIO14), Q8.1 (G)
unnamed: A1.20 (GPIO15), Q9.1 (G)
unnamed: A1.21 (GPIO16), J9.3
unnamed: A1.22 (GPIO17), J9.5
unnamed: A1.24 (GPIO18), J9.6
unnamed: A1.25 (GPIO19), J9.8
unnamed: A1.26 (GPIO20), Q3.1 (G)
unnamed: A1.27 (GPIO21), Q2.1 (G)
unnamed: A1.29 (GPIO22), Q1.1 (G)
unnamed: A2.4 (A1), J3.3
unnamed: A2.3 (A2), J3.4
unnamed: A2.5 (B1), J3.2
unnamed: A2.6 (B2), J3.1
unnamed: A3.4 (A1), J4.3
unnamed: A3.3 (A2), J4.4
unnamed: A3.5 (B1), J4.2
unnamed: A3.6 (B2), J4.1
unnamed: A4.4 (A1), J5.3
unnamed: A4.3 (A2), J5.4
unnamed: A4.5 (B1), J5.2
unnamed: A4.6 (B2), J5.1
unnamed: J6.7, Q9.2 (D)
unnamed: J6.8, Q1.2 (D)
unnamed: J7.7, Q8.2 (D)
unnamed: J7.8, Q2.2 (D)
unnamed: J8.7, Q7.2 (D)
unnamed: J8.8, Q3.2 (D)

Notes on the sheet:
i've had to sacrifice the continuity check due to lack of gpio :'(
place @ drv 3
IMU
place @ drv 1
steppers
GND
place @ drv 2
PWR
24V
t-plugs
terminals - place ideally at side of board
UART

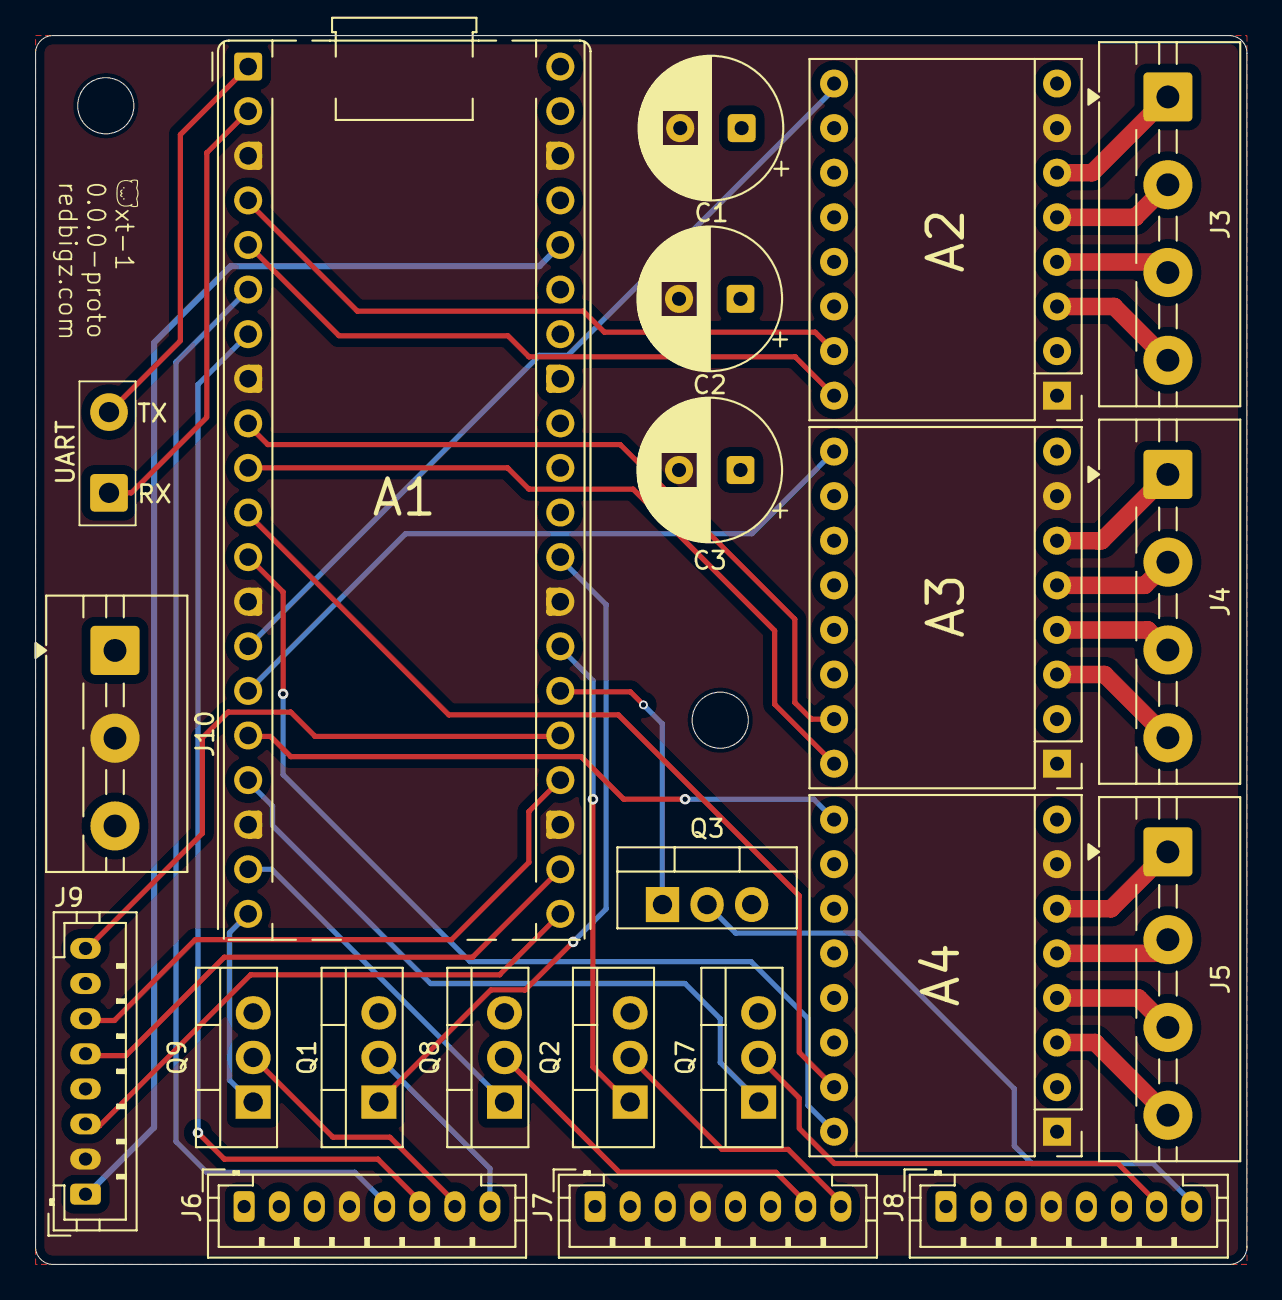
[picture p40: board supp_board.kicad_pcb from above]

Board: 4 copper layers, 69.0 x 70.0 mm, 24 parts (0 on the bottom side), 45 nets.

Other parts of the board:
REF1, REF2: MountingHole_3.2mm_M3
UART: Conn_01x02_Pin; SolderWire-0.5sqmm_1x02_P4.6mm_D0.9mm_OD2.1mm

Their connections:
/RX: UART.1; also elsewhere on the board
/TX: UART.2; also elsewhere on the board

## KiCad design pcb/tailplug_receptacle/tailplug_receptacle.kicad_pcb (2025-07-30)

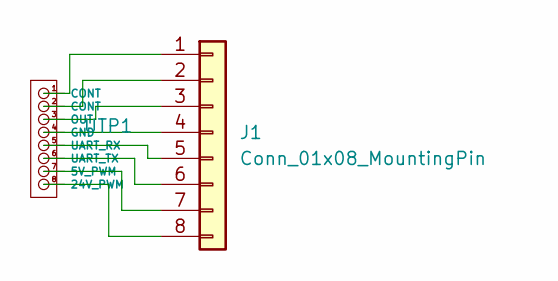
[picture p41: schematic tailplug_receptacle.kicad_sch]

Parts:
J1: Conn_01x08_MountingPin; JST_PH_S8B-PH-K_1x08_P2.00mm_Horizontal
UTP1: Tailplug_Female

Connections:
unnamed: J1.1, UTP1.1 (CONT)
unnamed: J1.2, UTP1.2 (CONT)
unnamed: J1.3, UTP1.3 (OUT)
unnamed: J1.4, UTP1.4 (GND)
unnamed: J1.5, UTP1.5 (UART_RX)
unnamed: J1.6, UTP1.6 (UART_TX)
unnamed: J1.7, UTP1.7 (5V_PWM)
unnamed: J1.8, UTP1.8 (24V_PWM)

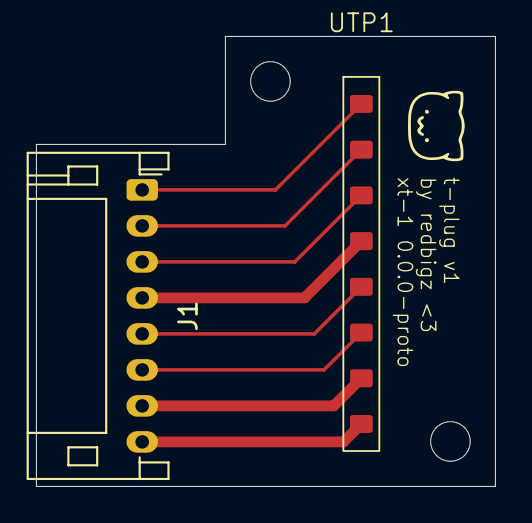
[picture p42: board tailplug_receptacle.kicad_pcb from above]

Board: 2 copper layers, 25.5 x 25.0 mm, 4 parts (0 on the bottom side), 8 nets.

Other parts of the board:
REF1, REF2: MountingHole_2.2mm_M2

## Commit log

2025-07-17 Add work from 2025-07-17
    [tailplug.kicad_pcb, tailplug.kicad_sch, tailplug_receptacle.kicad_pcb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]
2025-07-18 Add work from 2025-07-18
    [tailplug_receptacle.kicad_pcb, tailplug_receptacle.kicad_sch]
2025-07-19 Added toolhead mount fix update, added checklist
2025-07-20 Add work from 2025-07-20
    [tailplug.kicad_pcb, tailplug.kicad_sch]
2025-07-23 Add work from 2025-07-22 to 2025-07-23
    [supp_board.kicad_pcb, supp_board.kicad_sch]
2025-07-26 Add CAD Credits
2025-07-26 Add work from 2025-07-24 to 2025-07-26
    [supp_board.kicad_pcb, supp_board.kicad_sch]
2025-07-27 Add work from 2025-07-27
    [adxl_holder.kicad_pcb, adxl_holder.kicad_sch, supp_board.kicad_pcb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]
2025-07-29 Add work from 2025-07-28/29
    [BOM.csv, XT-1 Full Assembly.step]
2025-07-30 Add Pi Pico and Heat Shrink to BOM
    [BOM.csv]
2025-07-30 Round cents on BOM
    [BOM.csv]
2025-07-30 Propagate BOM to README
2025-07-30 Reroute supp. board
    [supp_board.kicad_pcb, supp_board.kicad_sch]
2025-07-30 Add supp. board image
2025-07-30 Replace boykissers on PCBs with my pfp (copyright reasons :3)
    [supp_board.kicad_pcb, tailplug.kicad_pcb, tailplug_receptacle.kicad_pcb]
2025-07-31 Add Pi Pico link to BOM
    [BOM.csv]
2025-08-02 Set stage to Approved
